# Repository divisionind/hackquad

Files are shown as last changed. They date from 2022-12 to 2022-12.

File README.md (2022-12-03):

# HackQuad
An open-source esp32-based IoT quadcopter intended to be controlled over WiFi (STA or AP) via an xbox controller.

### Why
I made this in 2020, early 2021, because I like building stuff and wanted to test my mechatronics / full-stack product development 
skills. I always planned on open-sourcing it. However, after I got it flying I moved on to other projects and forgot about it.
Today I decided it's about time. I didn't have the heart to clean it up much (kinda nostalgic for me now) so its still 
very much in that dirty development stage. I did organize it for the repo though. I hope this serves as a good reference for anyone
interested in what makes a minimal quadcopter tick -- from the ground up.

### Media
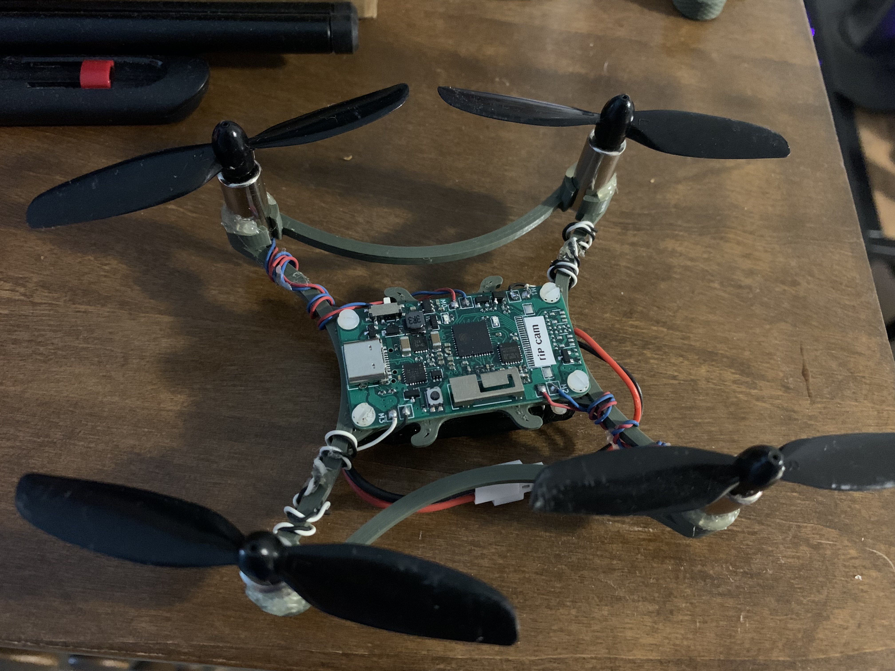
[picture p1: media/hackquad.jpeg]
hackquad

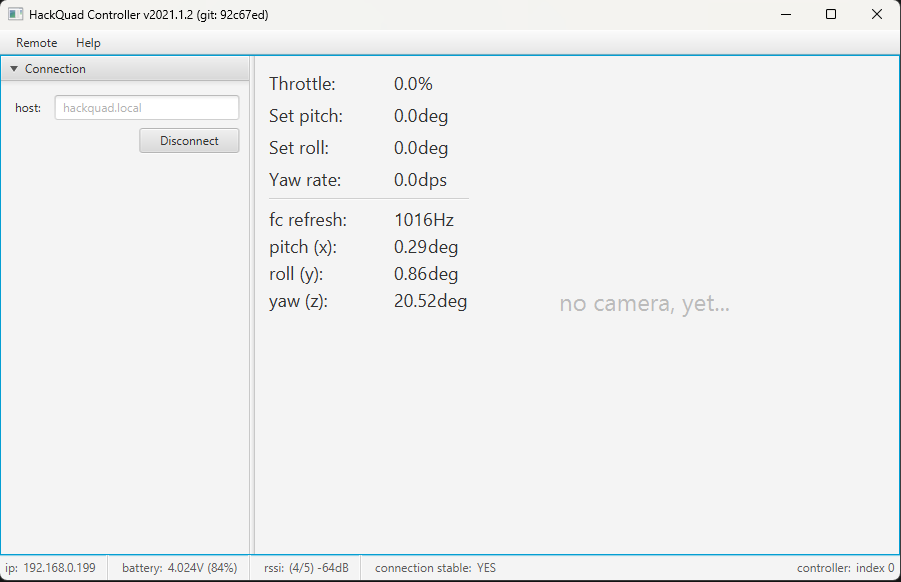
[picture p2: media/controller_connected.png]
controller connected

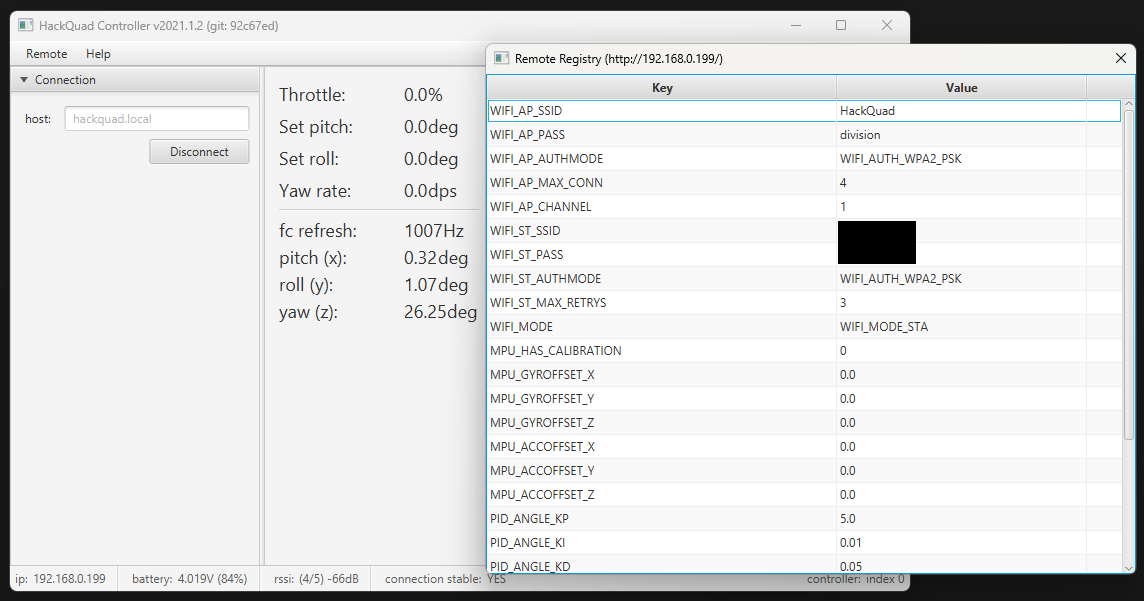
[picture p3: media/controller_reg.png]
controller registry

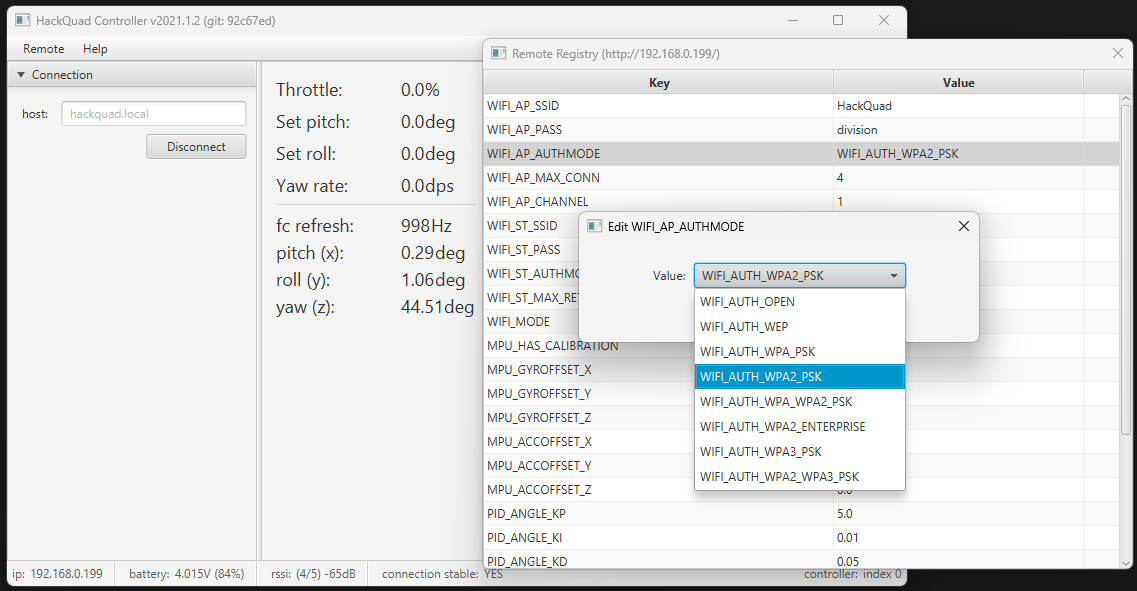
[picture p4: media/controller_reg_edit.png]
controller registry edit


#### [Flight test video](https://www.youtube.com/watch?v=RQggOqLySJw)

### Otherwise unlisted specs
|Part|Description|
|----|---|
|Battery|350mAh|
|Motors|8.5x20mm DC|
|Propellers|75mm D (60 works too)|
|USB-C|charging, programming & debugging|
|Frame|PLA+ here, ABS or other gummy polymer|

### Notes

#### The camera
I wired the camera connector up backwards like an idiot, but if you reverse the pin order it should work.

#### Possible improvements
Something to make this project more practical would be dropping the camera, adding a better imu w/ magnetometer, a several watt
RGB led, larger battery, maybe GPS, etc... and using the mesh networking capability of the espressif chips to make a very 
cheap drone light show platform. I say maybe GPS because dead-reckoning imu data combined w/ rssi info in a massive cluster might be
enough to get stable quad-to-quad relative positional information (saving on cost of the individual unit).

#### Improvements for this implementation
- neutral boyancy
- better IMU w/ magnometer
- proper multi-position IMU calibration routine to correct for axes skew
- linear acceleration control layer
- better battery capacity estimation

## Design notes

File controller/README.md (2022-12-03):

hackquad_controller
-------------------
The control software for the HackQuad open-source esp32-based quadcopter.
Proudly written in Java.

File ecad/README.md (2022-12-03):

# hackquad_hardware
The PCB revision says MK4, but I was being very liberal w/ what constitutes a version back then. This
was my 2nd ever PCB while learning electronics design, and I'd do a lot different today.

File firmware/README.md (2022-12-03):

hackquad_firmware
-----------------
The firmware for the hackquad esp32-based quadcopter.

### Build Instructions
1. Install IDF
2. Ensure you have dialout permissions `sudo usermod -a -G dialout $USER; sudo reboot`
3. Run `idf.py flash -b 921600` in a terminal initialized with IDF ENV.

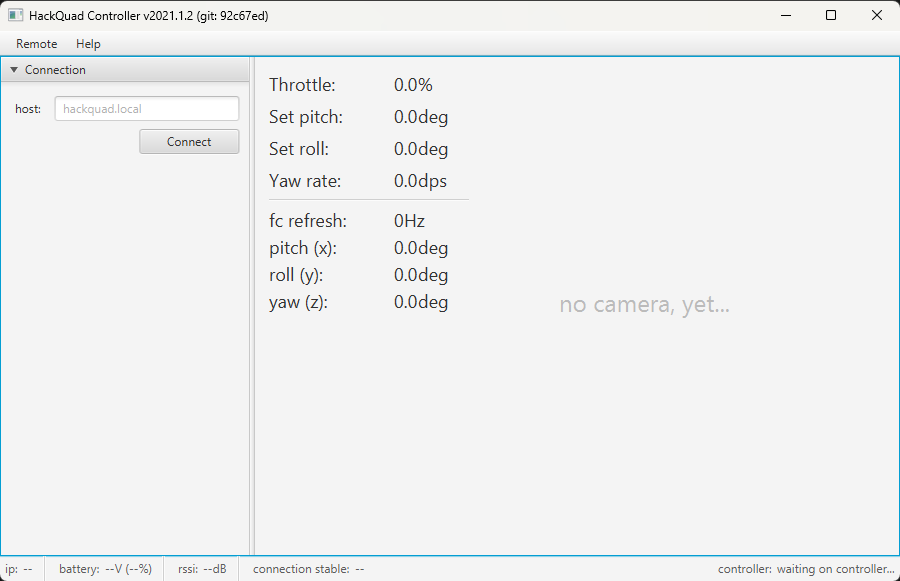
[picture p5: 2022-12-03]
media/controller_not_connected.png

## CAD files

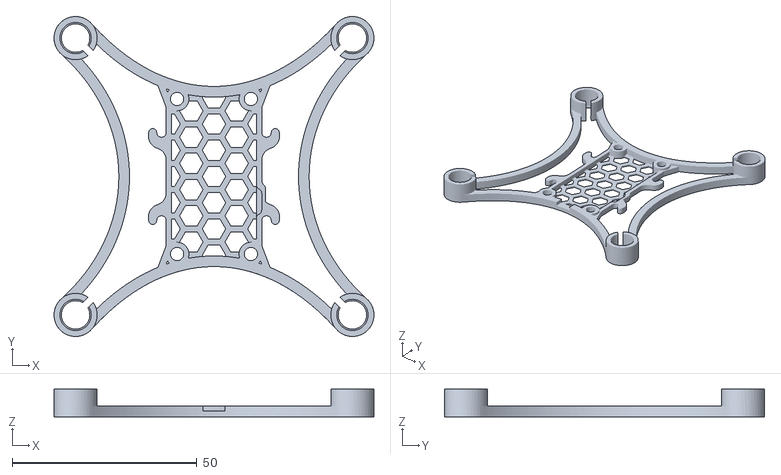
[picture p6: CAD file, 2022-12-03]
frame/modified_micro105.STL
86.7 x 86.7 x 7.50

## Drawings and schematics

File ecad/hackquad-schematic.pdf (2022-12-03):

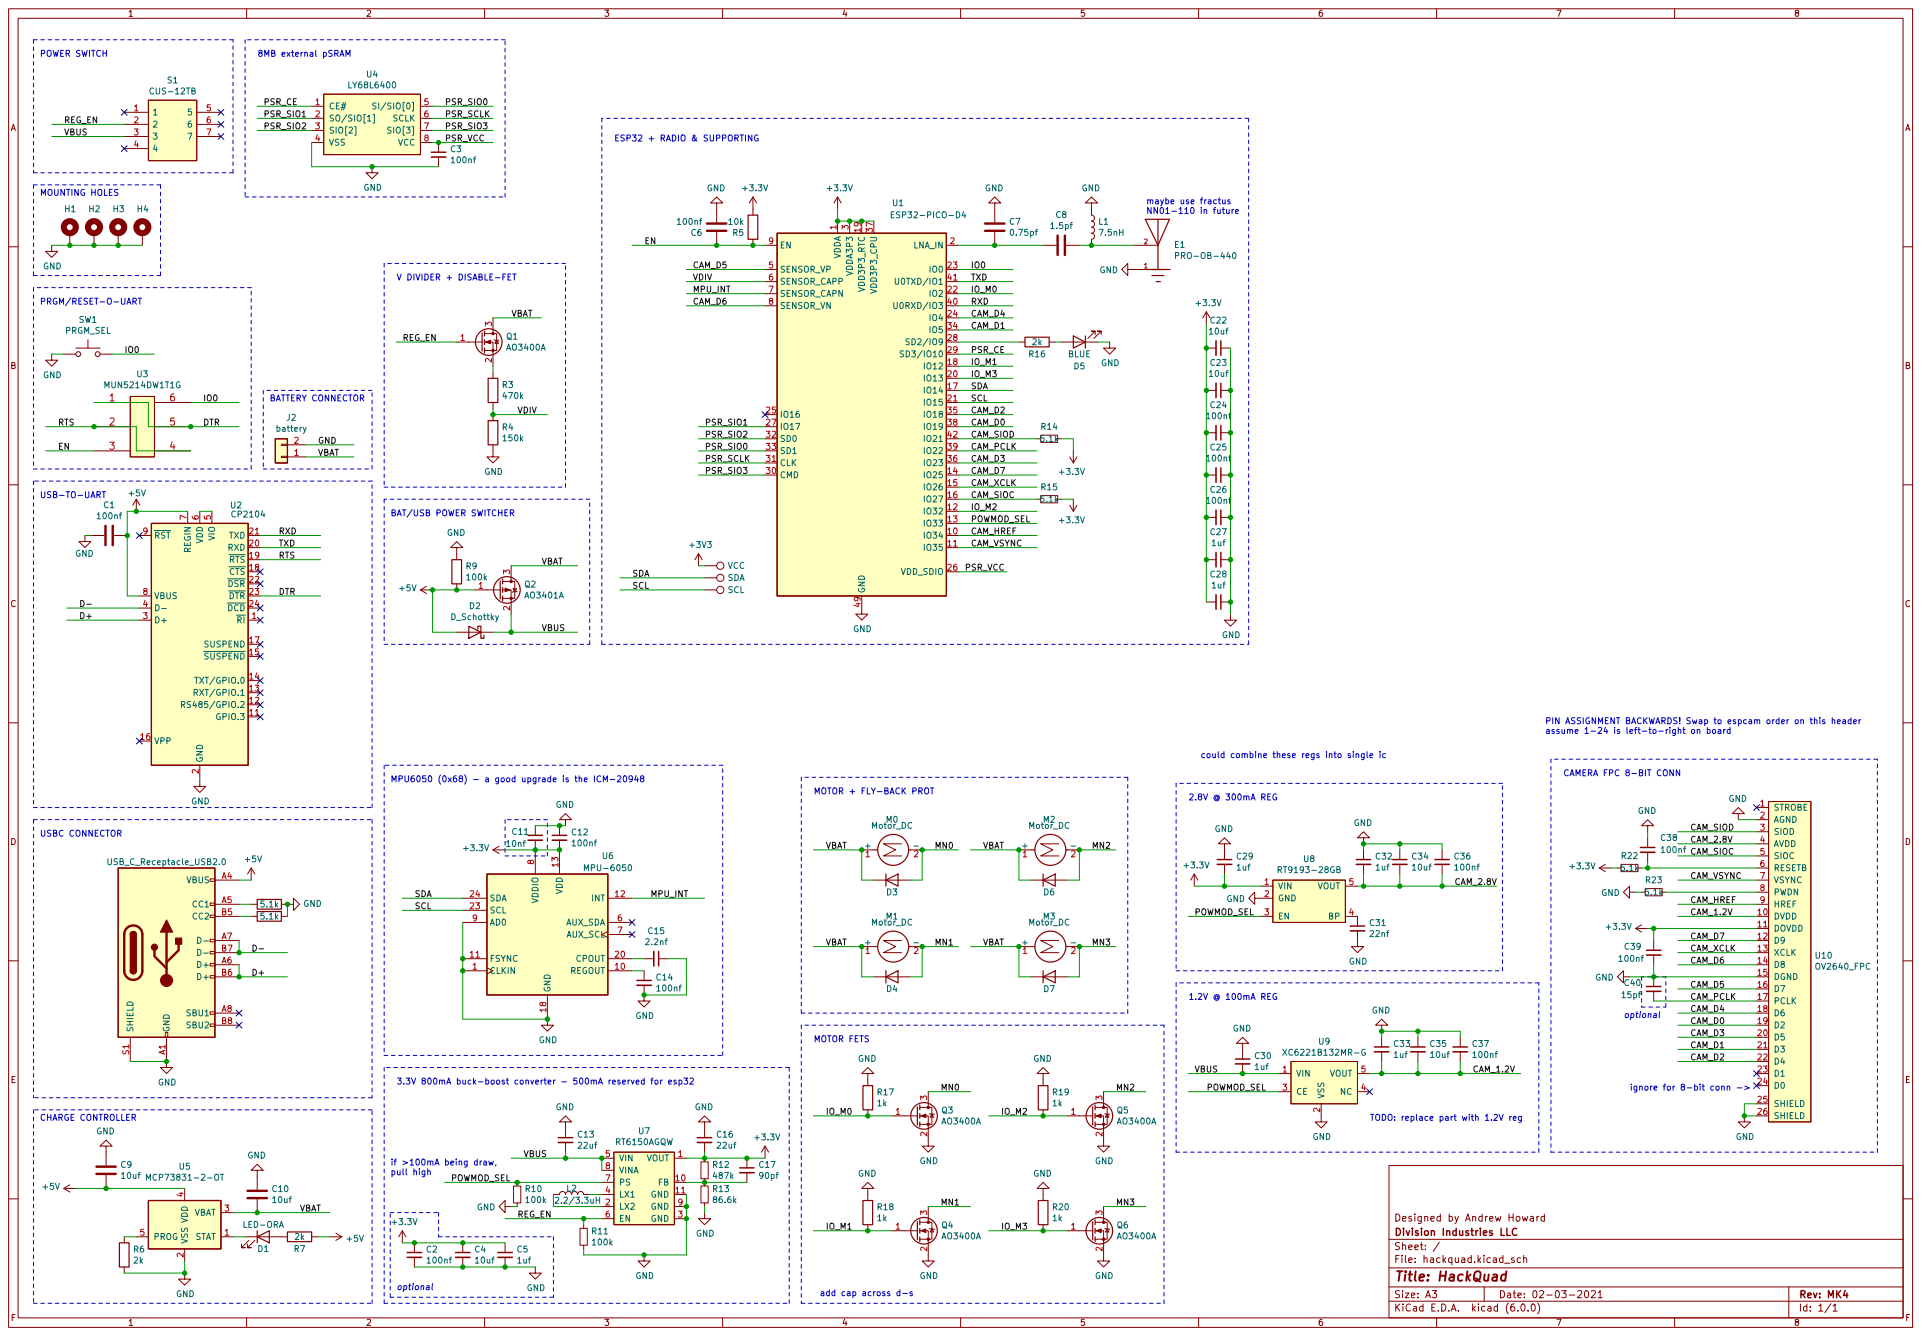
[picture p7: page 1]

PSR_SCLK
PSR_SIO3 PSR_VCC
V DIVIDER + DISABLE-FET MPU6050 (0x68) - a good upgrade is the ICM-20948

could combine these regs into single ic USB-TO-UART

7 VBUS 8 ~{RST} 9 U2CP2104 GND GND

BAT/USB POWER SWITCHER

2 RXD 20 TXD 21 ~{DSR}22 ~{DTR}23 ~{DCD}24 D+ 3 D- 4 VIO

PIN ASSIGNMENT BACKWARDS! Swap to espcam order on this header
assume 1-24 is left-to-right on board CAMERA FPC 8-BIT CONN

Designed by Andrew Howard GND

3.3V 800mA buck-boost converter - 500mA reserved for esp32

TODO: replace part with 1.2V reg

File: hackquad.kicad_sch Sheet: / Division Industries LLC

add cap across d-s optional

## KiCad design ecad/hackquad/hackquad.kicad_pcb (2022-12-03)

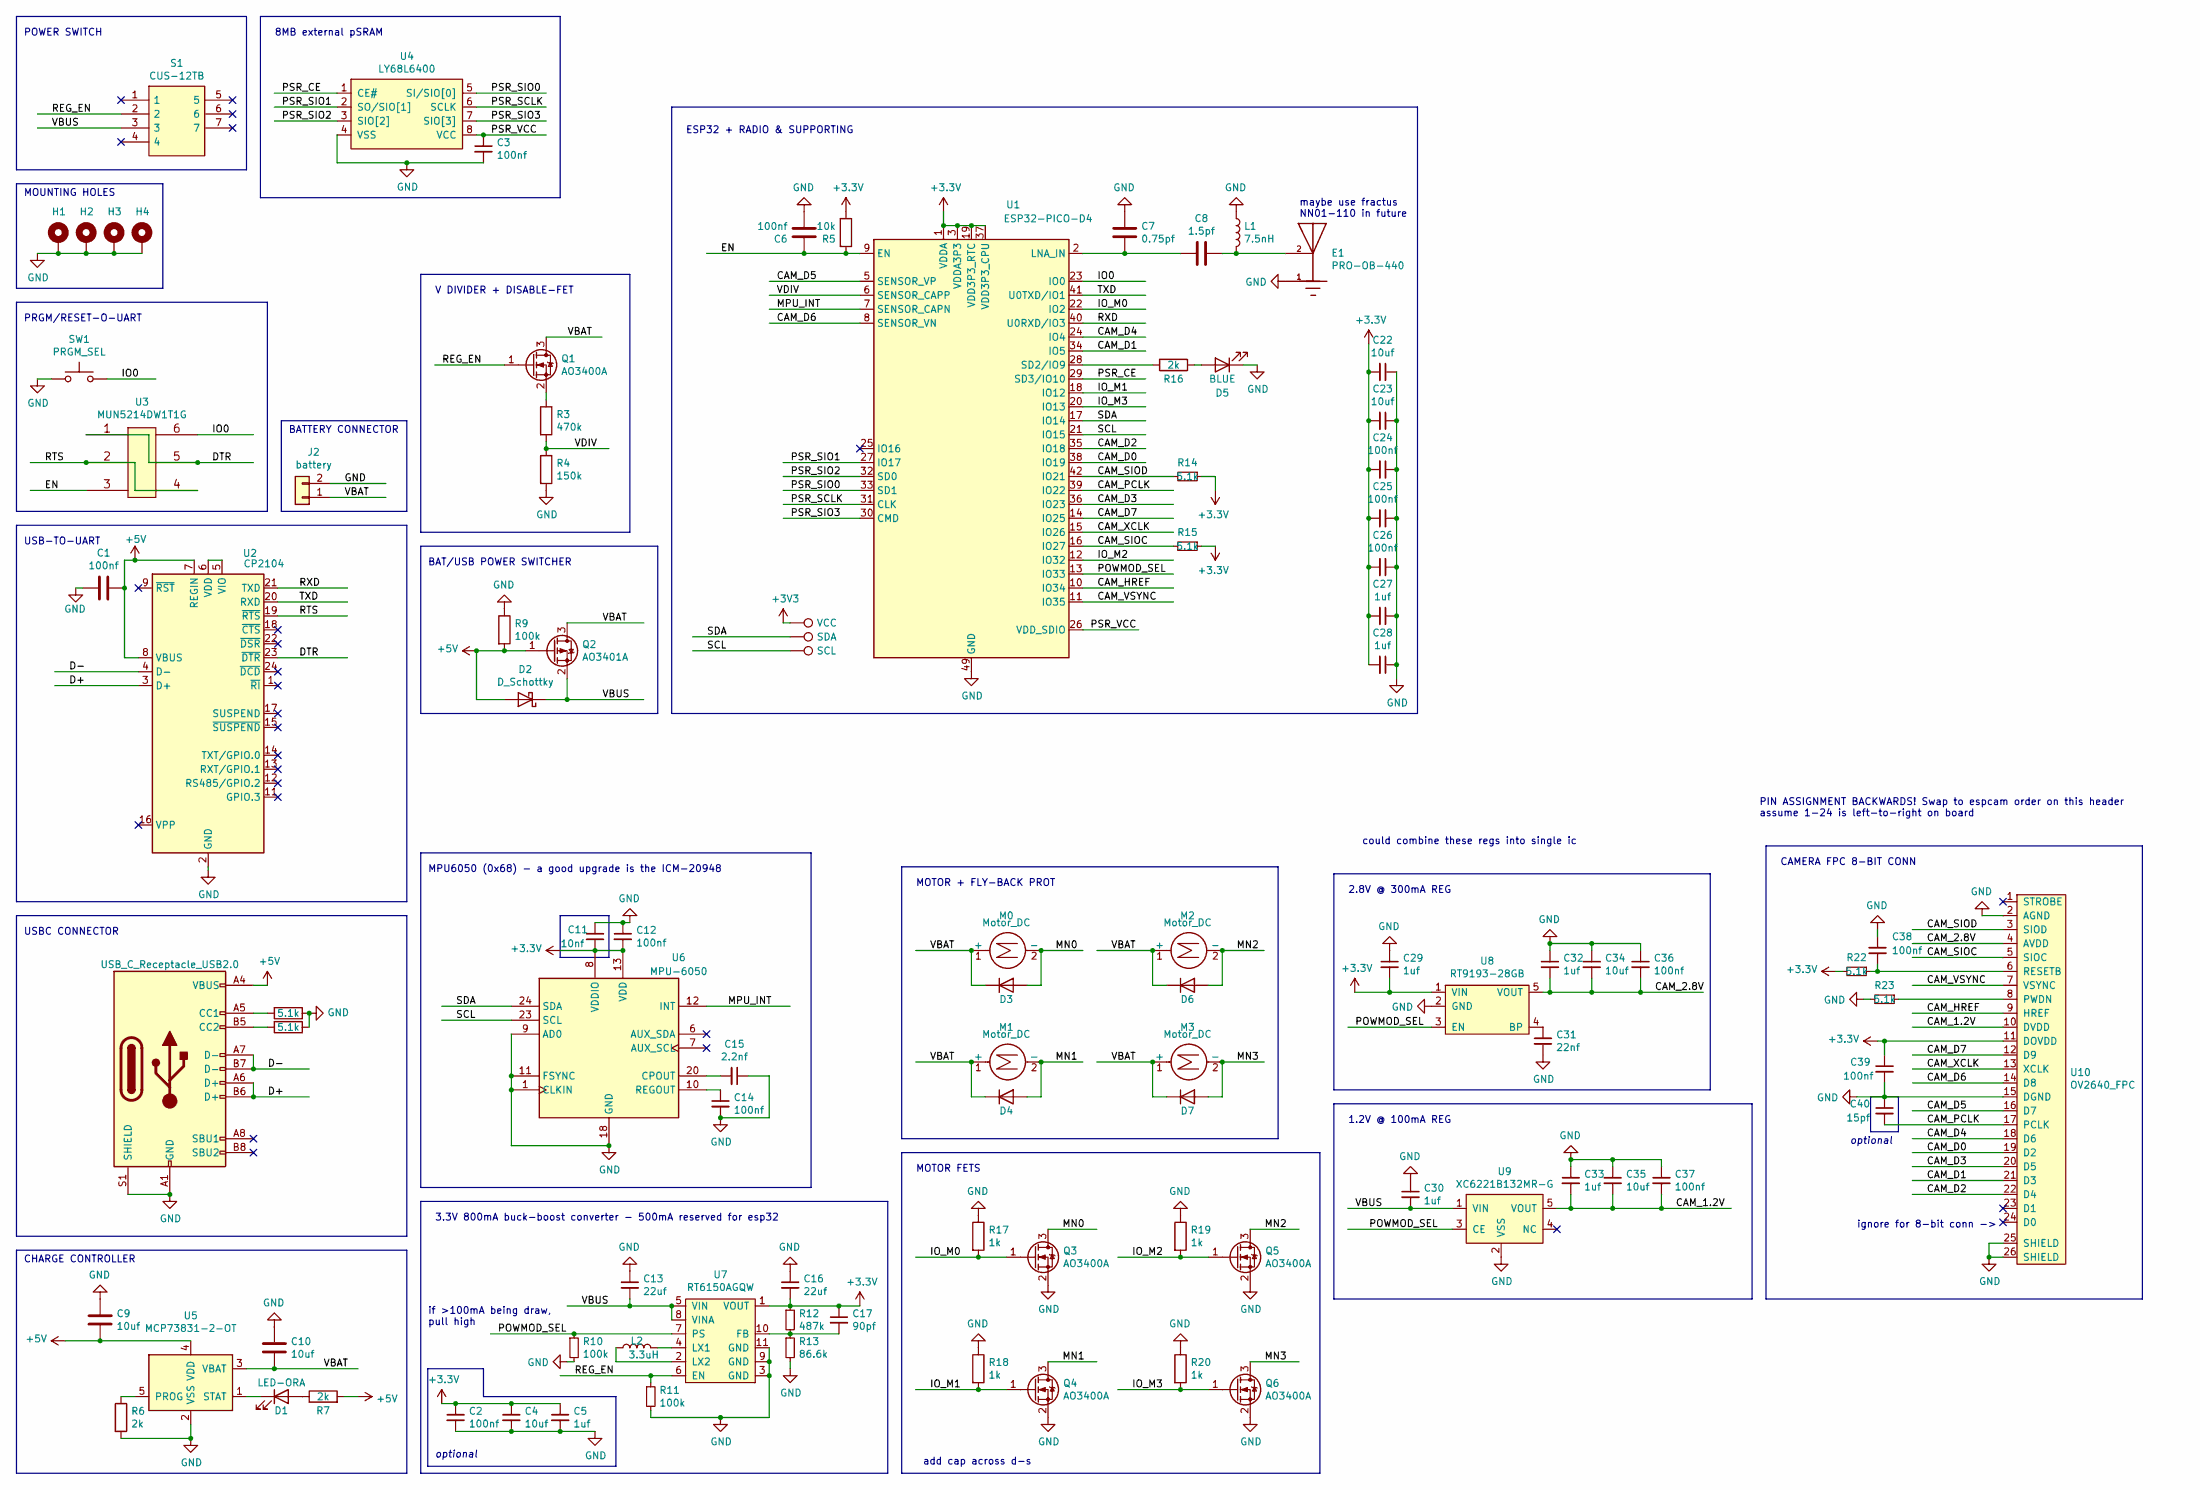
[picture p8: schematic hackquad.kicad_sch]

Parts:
C1, C2, C3, C6, C24, C25, C26, C36, C37, C38, C39: 100nf; C_0402_1005Metric
C4, C9, C10, C22, C23, C34, C35: 10uf; C_0402_1005Metric
C5, C27, C28, C29, C30, C32, C33: 1uf; C_0402_1005Metric
C7: 0.75pf; C_0402_1005Metric
C8: 1.5pf; C_0402_1005Metric
C11: 10nf; C_0402_1005Metric; LCSC C60133
C12, C14: 100nf; C_0402_1005Metric; LCSC C60474
C13, C16: 22uf; C_1206_3216Metric; LCSC C386064
C15: 2.2nf; C_0402_1005Metric; LCSC C513667
C17: 90pf; C_0402_1005Metric
C31: 22nf; C_0402_1005Metric
C40: 15pf; C_0402_1005Metric
D1: LED-ORA; LED_0603_1608Metric; LCSC C2286
D2: D_Schottky; D_SOD-123; LCSC` C8598
D3, D4, D6, D7: D; D_SOD-123F; LCSC C64898
D5: BLUE; LED_0603_1608Metric; LCSC C72041
E1: PRO-OB-440; ANT_PRO-OB-440; PARTREV 3.2
H1, H2, H3, H4: MountingHole_Pad; MountingHole_2.2mm_M2_Pad_Via
J1: USB_C_Receptacle_USB2.0; USB_C_Receptacle_HRO_TYPE-C-31-M-12; LCSC C165948
J2: battery; battery_pads
L1: 7.5nH; L_0402_1005Metric; LCSC C341696
L2: 3.3uH; L_4x4x3mm; LCSC C36409/C340390
M0, M1, M2, M3: Motor_DC; PinHeader_1x02_P2.54mm_Vertical
Q1, Q3, Q4, Q5, Q6: AO3400A; SOT-23
Q2: AO3401A; SOT-23; LCSC C347476
R1, R2, R14, R15, R22, R23: 5.1k; R_0402_1005Metric
R3: 470k; R_0402_1005Metric; LCSC C25790
R4: 150k; R_0402_1005Metric; LCSC C25755
R5: 10k; R_0402_1005Metric
R6, R7, R16: 2k; R_0402_1005Metric
R9, R10, R11: 100k; R_0402_1005Metric
R12: 487k; R_0402_1005Metric
R13: 86.6k; R_0402_1005Metric
R17, R18, R19, R20: 1k; R_0402_1005Metric
S1: CUS-12TB; CUS-12B; Manufacturer_Part_Number CUS-12TB
SW1: PRGM_SEL; pushbutton_TS-1185EC-C-D-B; LCSC C318893
TP1: VCC; TestPoint_Pad_D1.0mm
TP3: SDA; TestPoint_Pad_D1.0mm
TP4: SCL; TestPoint_Pad_D1.0mm
U1: ESP32-PICO-D4; QFN-48-1EP_7x7mm_P0.5mm_EP5.3x5.3mm
U2: CP2104; QFN-24-1EP_4x4mm_P0.5mm_EP2.6x2.6mm
U3: MUN5214DW1T1G; SOT-363_SC-70-6; LCSC C94403
U4: LY68L6400; SOP-8_3.9x4.9mm_P1.27mm; LCSC C261881
U5: MCP73831-2-OT; SOT-23-5; LCSC C424093
U6: MPU-6050; InvenSense_QFN-24_4x4mm_P0.5mm
U7: RT6150AGQW; WDFN-10L_3x3
U8: RT9193-28GB; SOT-23-5; LCSC C56731
U9: XC6221B132MR-G; SOT-23-5; LCSC C16613
U10: OV2640_FPC; FPC_24_AFC01-S24FCC-00; LCSC C262276

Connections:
+3V3: C2.1, C4.1, C5.1, C11.2, C12.2, C16.2, C17.1, C22.2, C23.2, C24.2, C25.2, C26.2, C27.2, C28.2, C29.2, C39.1, R5.2, R12.1, R14.1, R15.1, R22.2, TP1.1, U1.1 (VDDA), U1.3 (VDDA3P3), U1.4 (VDDA3P3), U1.19 (VDD3P3_RTC), U1.37 (VDD3P3_CPU), U1.43 (VDDA), U1.46 (VDDA), U6.8 (VDDIO), U6.13 (VDD), U7.1 (VOUT), U8.1 (VIN), U10.11 (DOVDD)
+5V: C1.1, C9.2, D2.2 (A), J1.A4 (VBUS), J1.A9 (VBUS), J1.B4 (VBUS), J1.B9 (VBUS), Q2.1 (G), R7.2, R9.2, U2.7 (REGIN), U2.8 (VBUS), U5.4 (VDD)
/CAM_1.2V: C33.2, C35.2, C37.2, U9.5 (VOUT), U10.10 (DVDD)
/CAM_2.8V: C32.2, C34.2, C36.2, U8.5 (VOUT), U10.4 (AVDD)
/CAM_D0: U1.38 (IO19), U10.19 (D2)
/CAM_D1: U1.34 (IO5), U10.21 (D3)
/CAM_D2: U1.35 (IO18), U10.22 (D4)
/CAM_D3: U1.36 (IO23), U10.20 (D5)
/CAM_D4: U1.24 (IO4), U10.18 (D6)
/CAM_D5: U1.5 (SENSOR_VP), U10.16 (D7)
/CAM_D6: U1.8 (SENSOR_VN), U10.14 (D8)
/CAM_D7: U1.14 (IO25), U10.12 (D9)
/CAM_HREF: U1.10 (IO34), U10.9 (HREF)
/CAM_PCLK: C40.2, U1.39 (IO22), U10.17 (PCLK)
/CAM_SIOC: R15.2, U1.16 (IO27), U10.5 (SIOC)
/CAM_SIOD: R14.2, U1.42 (IO21), U10.3 (SIOD)
/CAM_VSYNC: U1.11 (IO35), U10.7 (VSYNC)
/CAM_XCLK: U1.15 (IO26), U10.13 (XCLK)
/D+: J1.A6 (D+), J1.B6 (D+), U2.3 (D+)
/D-: J1.A7 (D-), J1.B7 (D-), U2.4 (D-)
/DTR: U2.23 (~DTR), U3.1, U3.5
/EN: C6.1, R5.1, U1.9 (EN), U3.3
/IO0: SW1.2, U1.23 (IO0), U3.6
/IO_M0: Q3.1 (G), R17.2, U1.22 (IO2)
/IO_M1: Q4.1 (G), R18.2, U1.18 (IO12)
/IO_M2: Q5.1 (G), R19.2, U1.12 (IO32)
/IO_M3: Q6.1 (G), R20.2, U1.20 (IO13)
/MN0: D3.2 (A), M0.2 (-), Q3.3 (D)
/MN1: D4.2 (A), M1.2 (-), Q4.3 (D)
/MN2: D6.2 (A), M2.2 (-), Q5.3 (D)
/MN3: D7.2 (A), M3.2 (-), Q6.3 (D)
/MPU_INT: U1.7 (SENSOR_CAPN), U6.12 (INT)
/POWMOD_SEL: R10.1, U1.13 (IO33), U7.7 (PS), U8.3 (EN), U9.3 (CE)
/PSR_CE: U1.29 (SD3/IO10), U4.1 (CE#)
/PSR_SCLK: U1.31 (CLK), U4.6 (SCLK)
/PSR_SIO0: U1.33 (SD1), U4.5 (SI/SIO[0])
/PSR_SIO1: U1.27 (IO17), U4.2 (SO/SIO[1])
/PSR_SIO2: U1.32 (SD0), U4.3 (SIO[2])
/PSR_SIO3: U1.30 (CMD), U4.7 (SIO[3])
/PSR_VCC: C3.1, U1.26 (VDD_SDIO), U4.8 (VCC)
/REG_EN: Q1.1 (G), R11.1, S1.2, U7.6 (EN)
/RTS: U2.19 (~RTS), U3.2, U3.4
/RXD: U1.40 (U0RXD/IO3), U2.21 (TXD)
/SCL: TP4.1, U1.21 (IO15), U6.23 (SCL)
/SDA: TP3.1, U1.17 (IO14), U6.24 (SDA)
/TXD: U1.41 (U0TXD/IO1), U2.20 (RXD)
/VBAT: C10.2, D3.1 (K), D4.1 (K), D6.1 (K), D7.1 (K), J2.1, M0.1 (+), M1.1 (+), M2.1 (+), M3.1 (+), Q1.3 (D), Q2.3 (D), U5.3 (VBAT)
/VBUS: C13.2, C30.2, D2.1 (K), Q2.2 (S), S1.3, U7.5 (VIN), U7.8 (VINA), U9.1 (VIN)
/VDIV: R3.2, R4.1, U1.6 (SENSOR_CAPP)
GND: C1.2, C2.2, C3.2, C4.2, C5.2, C6.2, C7.1, C9.1, C10.1, C11.1, C12.1, C13.1, C14.2, C15.1, C16.1, C22.1, C23.1, C24.1, C25.1, C26.1, C27.1, C28.1, C29.1, C30.1, C31.2, C32.1, C33.1, C34.1, C35.1, C36.1, C37.1, C38.1, C39.2, C40.1, D5.1 (K), E1.1, H1.1, H2.1, H3.1, H4.1, J1.A1 (GND), J1.A12 (GND), J1.B1 (GND), J1.B12 (GND), J1.S1 (SHIELD), J2.2, L1.1, Q3.2 (S), Q4.2 (S), Q5.2 (S), Q6.2 (S), R1.1, R2.1, R4.2, R6.2, R9.1, R10.2, R11.2, R13.2, R17.1, R18.1, R19.1, R20.1, R23.2, SW1.1, U1.49 (GND), U2.2 (GND), U2.25 (GND), U4.4 (VSS), U5.2 (VSS), U6.1 (CLKIN), U6.9 (AD0), U6.11 (FSYNC), U6.18 (GND), U7.3 (GND), U7.9 (GND), U7.11 (GND), U8.2 (GND), U9.2 (VSS), U10.2 (AGND), U10.15 (DGND), U10.25 (SHIELD), U10.26 (SHIELD)
unnamed: C7.2, C8.2, U1.2 (LNA_IN)
unnamed: C8.1, E1.2, L1.2
unnamed: C14.1, U6.10 (REGOUT)
unnamed: C15.2, U6.20 (CPOUT)
unnamed: C17.2, R12.2, R13.1, U7.10 (FB)
unnamed: C31.1, U8.4 (BP)
unnamed: C38.2, R22.1, U10.6 (RESETB)
unnamed: D1.1 (K), U5.1 (STAT)
unnamed: D1.2 (A), R7.1
unnamed: D5.2 (A), R16.1
unnamed: J1.A5 (CC1), R1.2
unnamed: J1.B5 (CC2), R2.2
unnamed: L2.1, U7.2 (LX2)
unnamed: L2.2, U7.4 (LX1)
unnamed: Q1.2 (S), R3.1
unnamed: R6.1, U5.5 (PROG)
unnamed: R16.2, U1.28 (SD2/IO9)
unnamed: R23.1, U10.8 (PWDN)
unnamed: U2.5 (VIO), U2.6 (VDD)

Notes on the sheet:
MPU6050 (0x68) - a good upgrade is the ICM-20948
CHARGE CONTROLLER
POWER SWITCH
1.2V @ 100mA REG
MOTOR FETS
MOUNTING HOLES
V DIVIDER + DISABLE-FET
MOTOR + FLY-BACK PROT
3.3V 800mA buck-boost converter - 500mA reserved for esp32
optional
if >100mA being draw, pull high
2.8V @ 300mA REG
add cap across d-s
USB-TO-UART
USBC CONNECTOR
8MB external pSRAM
PRGM/RESET-O-UART
PIN ASSIGNMENT BACKWARDS! Swap to espcam order on this header assume 1-24 is left-to-right on board
BATTERY CONNECTOR
BAT/USB POWER SWITCHER
CAMERA FPC 8-BIT CONN
maybe use fractus NN01-110 in future
ignore for 8-bit conn ->
could combine these regs into single ic
ESP32 + RADIO & SUPPORTING

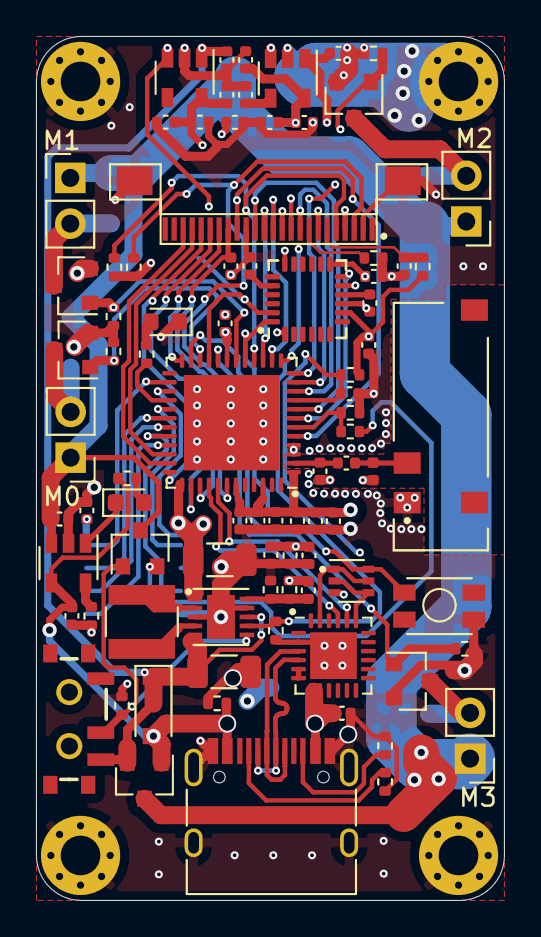
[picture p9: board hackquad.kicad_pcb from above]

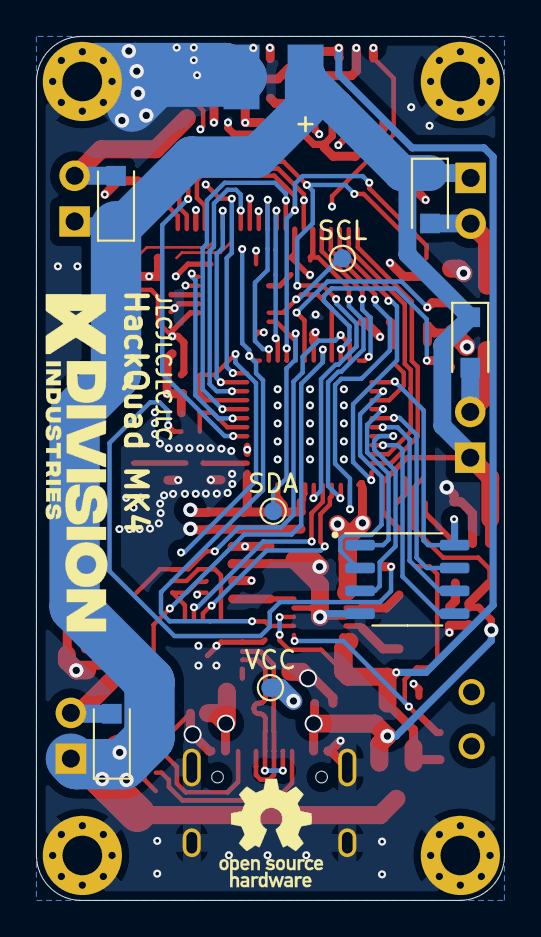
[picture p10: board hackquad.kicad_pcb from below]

Board: 4 copper layers, 26.0 x 48.0 mm, 98 parts (9 on the bottom side), 69 nets.

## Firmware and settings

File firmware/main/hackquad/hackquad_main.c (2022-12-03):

/*
 * HackQuad - an open-source firmware+hardware quadcopter
 * Copyright (C) 2020, Andrew Howard, <divisionind.com>
 *
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
 * You should have received a copy of the GNU General Public License
 * along with this program.  If not, see <https://www.gnu.org/licenses/>.
 */

#include <math.h>

#include "freertos/FreeRTOS.h"
#include "freertos/task.h"
#include "driver/gpio.h"
#include "mdns.h"
#include "esp_log.h"
#include "hackquad/motor.h"
#include "hackquad/registry.h"
#include "hackquad/battery.h"
#include "hackquad/wifi.h"
#include "hackquad/mpu.h"
#include "hackquad/hackquad_msg.h"
#include "hackquad/udpserver.h"
#include "hackquad/pid.h"
#include "hackquad/httpserver.h"
#include "hackquad/blinkcodes.h"
#include "pthread.h"

#define POWER_SEL_IO        33
#define HACKQUAD_MDNS_EN    1   /* whether or not to init mdns */
#define HACKQUAD_TEST_LOG   0   /* whether or not to spawn logging task */

#define FLAG_PANIC_MODE     (1 << 31)
#define FC_PANIC_MODE_ACT   50  /* max degrees of rotation before fc enters panic-mode */

#define STATUS_UPDATE_RATE  100  /* delay in ms between sending status updates */
#define FC_UPDATE_TIMEOUT   50   /* delay in ms between recv-ing updates before fc times-out */
#define NO_CTRL_TIMEOUT     3000 /* delay in ms to enter panic mode after not recving ctrl update */

/* copied strait from arduino cause im lazy */
#define constrain(amt, low, high) ((amt)<(low)?(low):((amt)>(high)?(high):(amt)))

struct control_data {
    float throttle, x, y, z;
    int flag_clear_panicmode;
};

TaskHandle_t task_hackquad_main;
float hq_avg_fcloop;

static struct control_data control;
static struct udp_context udp_ctx;
static struct pid_kon pid_angle_consts;
static struct pid_kon pid_rate_consts;
static struct pid_kon pid_yaw_rate_consts;
static pthread_mutex_t ctrl_mutex = PTHREAD_MUTEX_INITIALIZER;

static struct pid_ctx pid_angle[2] = {
        {.kons = &pid_angle_consts},
        {.kons = &pid_angle_consts}
};

static struct pid_ctx pid_rate[3] = {
        {.kons = &pid_rate_consts},
        {.kons = &pid_rate_consts},

        /* yaw, this needs different tuning parameters */
        {.kons = &pid_yaw_rate_consts}
};

static void hackquad_main(void *args) {
    (void) args;

    u32 msg;
    u64 curr_time, last_mpu_update = 0, last_fc_update = 0;
    float dt;
    struct control_data ctrl;
    float output[3];
    float x_set_point_adj;
    float y_set_point_adj;
    int fc_panicmode = 0;

    memset(&ctrl, 0, sizeof(ctrl));

    ESP_ERROR_CHECK(iic_init(0, I2C_BUS0_SDA, I2C_BUS0_SCL, I2C_BUS0_FRQ));
    mpu_init();

    /*if (!mpu_has_calibration) {
        ESP_LOGW(TAG, "MPU HAS NOT BEEN CALIBRATED! Flight will likely be unstable.");
    }*/

    // started, change blink-rate
    blc_setrate(BLCR_NORMAL);

    for (;;) {
        // on mpu or user-input data change, we re-do the flight calculations / update the motors
        if (xTaskNotifyWait(0, 0xFFFFFFFF, &msg, FC_UPDATE_TIMEOUT / portTICK_PERIOD_MS)) {

            // if new mpu data rdy, read data
            if (msg & HQMSG_MPU_UPDATE) {
                curr_time = esp_timer_get_time();
                mpu_read((float) (curr_time - last_mpu_update) * 1e-6f);
                last_mpu_update = curr_time;
            }

            // new control data rdy, read data
            if (msg & HQMSG_CTRL_UPDATE) {
                pthread_mutex_lock(&ctrl_mutex);
                memcpy(&ctrl, &control, sizeof(ctrl));
                pthread_mutex_unlock(&ctrl_mutex);
            }

            // use updated data to redo the flight calculations
            // calculate dt sense last fc update
            curr_time = esp_timer_get_time();
            dt = (float) (curr_time - last_fc_update) * 1e-6f;
            last_fc_update = curr_time;

            // keep track of avg flight controller refresh rate
            hq_avg_fcloop = hq_avg_fcloop * 0.995f + dt * 0.005f;

            /*
             * --=== FLIGHT CONTROLLER ===--
             */
            if (ctrl.throttle > 0) {
                // trigger panic mode if angle becomes too skewed
                if (fabsf(mpu_latest.angle.x) > FC_PANIC_MODE_ACT ||
                    fabsf(mpu_latest.angle.y) > FC_PANIC_MODE_ACT) {
                    fc_panicmode = 1;
                }

                // ensure motors shut off if in panic-mode
                if (ctrl.flag_clear_panicmode) {
                    fc_panicmode = 0;
                    blc_setrate(BLCR_NORMAL);
                } else
                if (fc_panicmode) {
                    blc_setrate(BLCR_VERY_FAST);
                    goto panic_mode;
                }

                // Rz(yaw)*in_setpoint
                // makes controls relative to world yaw==0, to make it easier to control while spinning (till i get yaw tuned)
                // likely suffers from angle roll-over issue
                //float yaw_rad = -mpu_latest.angle.z * DEG_TO_RAD;
                //float asx = ctrl.x * cosf(yaw_rad) + ctrl.y * sinf(yaw_rad);
                //float asy = -ctrl.x * sinf(yaw_rad) + ctrl.y * cosf(yaw_rad);

                x_set_point_adj = pid_update(&pid_angle[0], ctrl.x, mpu_latest.angle.x, dt);
                output[0] = pid_update(&pid_rate[0], -x_set_point_adj, mpu_latest.rate.x, dt);

                y_set_point_adj = pid_update(&pid_angle[1], ctrl.y, mpu_latest.angle.y, dt);
                output[1] = pid_update(&pid_rate[1], -y_set_point_adj, mpu_latest.rate.y, dt);

                // yaw always rate/gyro controlled
                output[2] = pid_update(&pid_rate[2], ctrl.z, mpu_latest.rate.z, dt);

                // TODO extend pid chain with linear acceleration control
                // TODO add multiplier for battery percentage adjustment
                // combine pid motor matrix
                motor_throttle(M0, constrain(ctrl.throttle - output[0] - output[1] - output[2], 0, 1023));
                motor_throttle(M1, constrain(ctrl.throttle - output[0] + output[1] + output[2], 0, 1023));
                motor_throttle(M2, constrain(ctrl.throttle + output[0] + output[1] - output[2], 0, 1023));
                motor_throttle(M3, constrain(ctrl.throttle + output[0] - output[1] + output[2], 0, 1023));
            } else {
                panic_mode:
                for (int i = 0; i < 4; i++)
                    motor_throttle(i, 0);
            }
        } else
            goto panic_mode; // timed-out (prob MPU issue), ensure motors remain off
    }
}

void udp_recv_handler(int id, u8 *data, size_t len) {
    switch (id) {
        default:
            ESP_LOGE(TAG, "packet of unknown id recv-ed, id = %i", id);
            break;

        /* UPDATE_CONTROL */
        case 69:
            if (len < 16)
                return;

            // pseudo-mutex created here by xTaskNotify() as we can be fairly confident that once notified, the flight
            // controller loop will process this WAY before our next control data update
            // could modify the data and cause problems
            pthread_mutex_lock(&ctrl_mutex);
            control.throttle = ((float *) data)[0] * MOTOR_MAX_THROTTLE;
            control.x        = ((float *) data)[1];
            control.y        = ((float *) data)[2];
            control.z        = ((float *) data)[3];

            // TODO create u8 flags var which stores clear panic mode and en stabilization info
            //      or keep as is and maintain stabilization for some period after zero throttle
            //      maybe use accel values and maintain stabilization until down-accel is zero

            // use sign bit to indicate that we wish to reset panic-mode detection
            control.flag_clear_panicmode = *((u32 *) &control.throttle) & FLAG_PANIC_MODE;
            *((u32 *) &control.throttle) &= ~FLAG_PANIC_MODE;
            pthread_mutex_unlock(&ctrl_mutex);

            // notify new data
            xTaskNotify(task_hackquad_main, HQMSG_CTRL_UPDATE, eSetBits);
            portYIELD();
            break;
    }
}

/**
 * Dont really need a separate task here if sockets support polling. Could just
 * recv and handle in the hackquad_main task.
 *
 * It would save on a lot of unnecessary mov's.
 */
static void udp_server_task(void *arg) {
    (void) arg;

    udp_ctx.recv_handler = udp_recv_handler;
    udp_create(&udp_ctx, IPADDR_ANY, UDPSERVER_PORT);

    for (;;)
        udp_yield(&udp_ctx);
}

#if HACKQUAD_TEST_LOG
static void test_log_task(void *arg) {
    (void) arg;

    for (;;) {
        //printf("fc = %.2f ms, \tx = %.2f, \ty = %.2f, \trx = %.2f, \try = %.2f\n", hq_avg_fcloop * 1000.0f, mpu_latest.angle[0], mpu_latest.angle[1], mpu_latest.rate[0], mpu_latest.rate[1]);
        printf("ax = %.5f, \tay = %.5f, \taz = %.5f, \tpitch = %.2f, \troll = %.2f\n", mpu_latest.raw_acc[0], mpu_latest.raw_acc[1], mpu_latest.raw_acc[2], mpu_latest.angle[0], mpu_latest.angle[1]);
        vTaskDelay(75 / portTICK_PERIOD_MS);
    }
}
#endif

static void hq_mdns_init() {
    // pretty slow
    /* without mdns in AP mode
        Ping statistics for 192.168.4.1:
            Packets: Sent = 50, Received = 50, Lost = 0 (0% loss),
        Approximate round trip times in milli-seconds:
            Minimum = 1ms, Maximum = 25ms, Average = 2ms
     */

    /* with mdns in AP mode
        Ping statistics for 192.168.4.1:
            Packets: Sent = 50, Received = 49, Lost = 1 (2% loss),
        Approximate round trip times in milli-seconds:
            Minimum = 1ms, Maximum = 39ms, Average = 3ms
     */
    mdns_txt_item_t mdns_txts[] = {
            {"board", "esp32"},
            {"path",  "/"}
    };

    ESP_ERROR_CHECK(mdns_init());
    ESP_ERROR_CHECK(mdns_hostname_set("hackquad"));
    ESP_ERROR_CHECK(mdns_instance_name_set("hackquad"));
    ESP_ERROR_CHECK(mdns_service_add("_webserver", "_http", "_tcp", 80, mdns_txts,
                                     sizeof(mdns_txts) / sizeof(mdns_txt_item_t)));
}

static void status_update_task(void *arg) {
    (void) arg;

    struct __attribute__((packed)) {
        u8 id;
        float battery;
        s8 rssi;
        float fc_loop_time;
        float x, y, z;
    } status_update;

    status_update.id = 20;

    for (;;) {
        status_update.battery = battery_read();
        status_update.rssi = wifi_get_rssi();
        status_update.fc_loop_time = hq_avg_fcloop;
        status_update.x = mpu_latest.angle.x;
        status_update.y = mpu_latest.angle.y;
        status_update.z = mpu_latest.angle.z;

        udp_sendp(&udp_ctx, (u8 * ) & status_update, sizeof(status_update));
        vTaskDelay(STATUS_UPDATE_RATE / portTICK_PERIOD_MS);
    }
}

void app_main() {
    motor_init();
    blc_init();

    // enable high-power mode (also turns on camera circuitry)
    //gpio_reset_pin(POWER_SEL_IO);
    //gpio_set_level(POWER_SEL_IO, 1);

    reg_init();
    battery_init();
    wifi_init();
#if HACKQUAD_MDNS_EN
    hq_mdns_init();
#endif
    http_init();

    xTaskCreate(hackquad_main, "hackquad_main", 4096, NULL, configMAX_PRIORITIES - 1, &task_hackquad_main);
    xTaskCreate(udp_server_task, "udp_server", 2048, NULL, configMAX_PRIORITIES - 2, NULL);
    xTaskCreate(status_update_task, "status_task", 2048, NULL, configMAX_PRIORITIES - 3, NULL);
#if HACKQUAD_TEST_LOG
    xTaskCreate(test_log_task, "log_task", 2048, NULL, 0, NULL);
#endif
}

DEFINE_REGISTRY({
    {"WIFI_AP_SSID",       REG_STR, &wifi_ap_ssid, 0, {0}},
    {"WIFI_AP_PASS",       REG_STR, &wifi_ap_pass, 0, {0}},
    {"WIFI_AP_AUTHMODE",   REG_8B,  &wifi_ap_authmode, 0, {0}},
    {"WIFI_AP_MAX_CONN",   REG_8B,  &wifi_ap_max_connection, 0, {0}},
    {"WIFI_AP_CHANNEL",    REG_8B,  &wifi_ap_channel, 0, {0}},
    {"WIFI_ST_SSID",       REG_STR, &wifi_st_ssid, 0, {0}},
    {"WIFI_ST_PASS",       REG_STR, &wifi_st_pass, 0, {0}},
    {"WIFI_ST_AUTHMODE",   REG_8B,  &wifi_st_authmode, 0, {0}},
    {"WIFI_ST_MAX_RETRYS", REG_8B,  &wifi_st_max_retrys, 0, {0}},
    {"WIFI_MODE",          REG_8B,  &wifi_mode, 0, {0}},

    {"MPU_HAS_CALIBRATION", REG_8B,  &mpu_has_calibration, 0, {0}},
    {"MPU_GYROFFSET_X",     REG_FLT, &mpu_gyroffset_x, 0, {0}},
    {"MPU_GYROFFSET_Y",     REG_FLT, &mpu_gyroffset_y, 0, {0}},
    {"MPU_GYROFFSET_Z",     REG_FLT, &mpu_gyroffset_z, 0, {0}},
    {"MPU_ACCOFFSET_X",     REG_FLT, &mpu_accoffset_x, 0, {0}},
    {"MPU_ACCOFFSET_Y",     REG_FLT, &mpu_accoffset_y, 0, {0}},
    {"MPU_ACCOFFSET_Z",     REG_FLT, &mpu_accoffset_z, 0, {0}},

    {"PID_ANGLE_KP",      REG_FLT, &pid_angle_consts.kp, 0, {0}},
    {"PID_ANGLE_KI",      REG_FLT, &pid_angle_consts.ki, 0, {0}},
    {"PID_ANGLE_KD",      REG_FLT, &pid_angle_consts.kd, 0, {0}},
    {"PID_ANGLE_EPSILON", REG_FLT, &pid_angle_consts.epsilon, 0, {0}},
    {"PID_RATE_KP",       REG_FLT, &pid_rate_consts.kp, 0, {0}},
    {"PID_RATE_KI",       REG_FLT, &pid_rate_consts.ki, 0, {0}},
    {"PID_RATE_KD",       REG_FLT, &pid_rate_consts.kd, 0, {0}},
    {"PID_RATE_EPSILON",  REG_FLT, &pid_rate_consts.epsilon, 0, {0}},
    {"PID_YAWRATE_KP",    REG_FLT, &pid_yaw_rate_consts.kp, 0, {0}},
});

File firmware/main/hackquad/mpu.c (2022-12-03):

/*
 * HackQuad - an open-source firmware+hardware quadcopter
 * Copyright (C) 2020, Andrew Howard, <divisionind.com>
 *
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
 * You should have received a copy of the GNU General Public License
 * along with this program.  If not, see <https://www.gnu.org/licenses/>.
 */

#include <math.h>
#include <string.h>
#include <stdbool.h>

#include "hackquad/mpu.h"
#include "hackquad/i2c.h"
#include "freertos/FreeRTOS.h"
#include "freertos/task.h"
#include "freertos/event_groups.h"
#include "driver/gpio.h"
#include "esp_log.h"
#include "hackquad/hackquad_msg.h"

/* 0=madgwick / 1=adaptive_comp_filter */
#define ANGLE_MODE 0

/* r/w macros for i2c */
#define iicw(reg, data)      iic_write(&mpu, reg, data)
#define iicr(reg, buff, len) iic_read(&mpu, reg, buff, len)

#define MPU_GYR_COMPFILTER0 0.7f
#define MPU_GYR_COMPFILTER1 0.3f

/*
 * ACC: 1 = +/-4g (8192 LSB/g) | 2 = +/-8g (4096 LSB/g) | 3 = +/-16g (2048 LSB/g)
 * GYR: 1 = +/-500 dps (65.5 LSB/dps) | 2 = +/-1000 dps (32.8 LSB/dps) | 3 = +/-2000 dps (16.4 LSB/dps)
 */
#define ACC_RANGE_SEL 2
#define ACC_LSB       4096.0f
#define GYR_RANGE_SEL 1
#define GYR_LSB       65.5f

/* gravitational acceleration in m/s^2 */
#define G_ACCL 9.80665f
#define ACC_TO_MSS ((1.0f / ACC_LSB) * G_ACCL)

#define MADGWICK_GYRO_ERR 5.f

/* REGISTRY */
u8 mpu_has_calibration = 0;
float mpu_gyroffset_x  = 0.0f;
float mpu_gyroffset_y  = 0.0f;
float mpu_gyroffset_z  = 0.0f;
float mpu_accoffset_x  = 0.0f;
float mpu_accoffset_y  = 0.0f;
float mpu_accoffset_z  = 0.0f;

struct mpu_data mpu_latest;

static iic_device_t mpu = {
    .address = MPU_ADDR,
    .port    = MPU_BUS
};

static inline void _mpu_read_raw() {
    u8  buff[14];
    s16 raw_acc16[3];
    s16 raw_gyr16[3];

    iicr(0x3B /* ACCEL_OUT */, buff, sizeof(buff)); // p29

    raw_acc16[0] = (buff[0] << 8) | buff[1];
    raw_acc16[1] = (buff[2] << 8) | buff[3];
    raw_acc16[2] = (buff[4] << 8) | buff[5];

    raw_gyr16[0] = (buff[8]  << 8) | buff[9];
    raw_gyr16[1] = (buff[10] << 8) | buff[11];
    raw_gyr16[2] = (buff[12] << 8) | buff[13];

    // dont need to divide raw_acc by LSB if only using values for angle calculations
    // this is because these calculations are interested in the distribution
    // of gravitational acceleration amongst the axes (e.g. they are unitless)
    mpu_latest.raw_acc.x = (float) raw_acc16[0] * ACC_TO_MSS;
    mpu_latest.raw_acc.y = (float) raw_acc16[1] * ACC_TO_MSS;
    mpu_latest.raw_acc.z = (float) raw_acc16[2] * ACC_TO_MSS;

    mpu_latest.raw_gyr.x = (float) raw_gyr16[0] / GYR_LSB;
    mpu_latest.raw_gyr.y = (float) raw_gyr16[1] / GYR_LSB;
    mpu_latest.raw_gyr.z = (float) raw_gyr16[2] / GYR_LSB;
}

#if ANGLE_MODE == 0
void mpu_read(float dt) {
    _mpu_read_raw();

    // update quaternion from rotation during elapsed time
    // TODO converges very slowly after crash, inc beta during rest to inc conv
    madgwick_update(&mpu_latest.ahrs, dt, mpu_latest.raw_acc.x, mpu_latest.raw_acc.y, mpu_latest.raw_acc.z,
                    mpu_latest.raw_gyr.x * DEG_TO_RAD, mpu_latest.raw_gyr.y * DEG_TO_RAD, mpu_latest.raw_gyr.z * DEG_TO_RAD);

    // take 70% of current accepted gyr and add it to 30% of new-raw gyr
    mpu_latest.rate.x = mpu_latest.rate.x * MPU_GYR_COMPFILTER0 + mpu_latest.raw_gyr.x * MPU_GYR_COMPFILTER1;
    mpu_latest.rate.y = mpu_latest.rate.y * MPU_GYR_COMPFILTER0 + mpu_latest.raw_gyr.y * MPU_GYR_COMPFILTER1;
    mpu_latest.rate.z = mpu_latest.rate.z * MPU_GYR_COMPFILTER0 + mpu_latest.raw_gyr.z * MPU_GYR_COMPFILTER1;

    // rpy angle
    vec3f_t gravity;
    quaternion_get_gravity(&mpu_latest.ahrs.q, &gravity);
    quaternion_euler(&mpu_latest.ahrs.q, &gravity, &mpu_latest.angle);
}
#elif ANGLE_MODE == 1
void mpu_read(float dt) {
    _mpu_read_raw();

    float comp_gyr, comp_acc = 0.006f, acc_err;
    const float comp_gain = 4.f;

    // error from g-vector
    acc_err = (sqrtf(mpu_latest.raw_acc.x*mpu_latest.raw_acc.x + mpu_latest.raw_acc.y*mpu_latest.raw_acc.y + mpu_latest.raw_acc.z*mpu_latest.raw_acc.z) / G_ACCL) - 1.f;
    acc_err = sqrtf(acc_err*acc_err);
    comp_acc *= 1.f / expf(acc_err*comp_gain);
    comp_gyr = 1.f - comp_acc;

    mpu_latest.angle.x = (mpu_latest.angle.x + mpu_latest.raw_gyr.x * dt) * comp_gyr +
                         ((atan2f(mpu_latest.raw_acc.y, mpu_latest.raw_acc.z) * RAD_TO_DEG) * comp_acc);
    mpu_latest.angle.y = (mpu_latest.angle.y + mpu_latest.raw_gyr.y * dt) * comp_gyr +
                         ((atanf(-mpu_latest.raw_acc.x / sqrtf(mpu_latest.raw_acc.y * mpu_latest.raw_acc.y + mpu_latest.raw_acc.z * mpu_latest.raw_acc.z)) * RAD_TO_DEG) * comp_acc);

    // filter gyro rates
    mpu_latest.rate.x = mpu_latest.rate.x * MPU_GYR_COMPFILTER0 + mpu_latest.raw_gyr.x * MPU_GYR_COMPFILTER1;
    mpu_latest.rate.y = mpu_latest.rate.y * MPU_GYR_COMPFILTER0 + mpu_latest.raw_gyr.y * MPU_GYR_COMPFILTER1;
    mpu_latest.rate.z = mpu_latest.rate.z * MPU_GYR_COMPFILTER0 + mpu_latest.raw_gyr.z * MPU_GYR_COMPFILTER1;
}
#endif

static void IRAM_ATTR _mpu_isr_handler(void *arg) {
    (void) arg;

    BaseType_t higher_priority_taskwoken /*= pdFALSE*/;

    //prvClearInterrupt(); // auto-clr

    // notify task of mpu update
    xTaskNotifyFromISR(task_hackquad_main, HQMSG_MPU_UPDATE, eSetBits, &higher_priority_taskwoken);

    // request ctx switch from kernel to notified task. for speeeeddd
    // assuming higher_priority_taskwoken always true, because it should be
    portYIELD_FROM_ISR();
}

int mpu_init() {
    u8 whoami;
    gpio_config_t isrconf;

    ESP_LOGI(TAG, "initializing mpu...");

    madgwick_init(&mpu_latest.ahrs, MADGWICK_GYRO_ERR);

    iicw(0x6B /* PWR_MGMT_1 */, 1 << 7 /* RESET */);
    vTaskDelay(120 / portTICK_PERIOD_MS);

    iicw(0x6B /* PWR_MGMT_1 */, 1 /* CLKSEL PLL gyro_x */);
    vTaskDelay(15 / portTICK_PERIOD_MS);
    iicw(0x1B /* GYRO_CONFIG */, (GYR_RANGE_SEL << 3) /* 1 = FS_SEL 500dps */);
    iicw(0x1C /* ACCEL_CONFIG */, (ACC_RANGE_SEL << 3) /* 2 = AFS_SEL 8g | 1 = AFS_SEL 4g */);
    iicw(0x1A /* CONFIG */, 3 /* DLPF_44_42 */);

    iicw(0x37 /* INT_PIN_CFG */, 1 << 4 /* clear INT_STATUS by any read */);
    iicw(0x38 /* INT_ENABLE */, 1 /* DATA_RDY_EN */);

    iicr(0x75 /* WHO_AM_I */, &whoami, 1);

    if (whoami == 0x68) {
        memset(&isrconf, 0, sizeof(isrconf));
        isrconf.pull_down_en = 1;
        isrconf.mode = GPIO_MODE_INPUT;
        isrconf.intr_type = GPIO_INTR_POSEDGE;
        isrconf.pin_bit_mask = 1ull << MPU_INT;

        ESP_ERROR_CHECK(gpio_reset_pin(MPU_INT));
        ESP_ERROR_CHECK(gpio_config(&isrconf));

        ESP_ERROR_CHECK(gpio_install_isr_service(0));
        ESP_ERROR_CHECK(gpio_isr_handler_add(MPU_INT, _mpu_isr_handler, NULL));

        return 0;
    } else
        return whoami;
}

static void IRAM_ATTR _mpu_calibrate_isr_handler(EventGroupHandle_t event) {
    BaseType_t higher_priority_taskwoken /*= pdFALSE*/;

    xEventGroupSetBitsFromISR(event, 1, &higher_priority_taskwoken);
    portYIELD_FROM_ISR();
}
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

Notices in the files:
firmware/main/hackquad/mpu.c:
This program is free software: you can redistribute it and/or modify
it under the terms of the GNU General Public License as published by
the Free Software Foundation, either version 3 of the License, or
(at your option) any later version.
